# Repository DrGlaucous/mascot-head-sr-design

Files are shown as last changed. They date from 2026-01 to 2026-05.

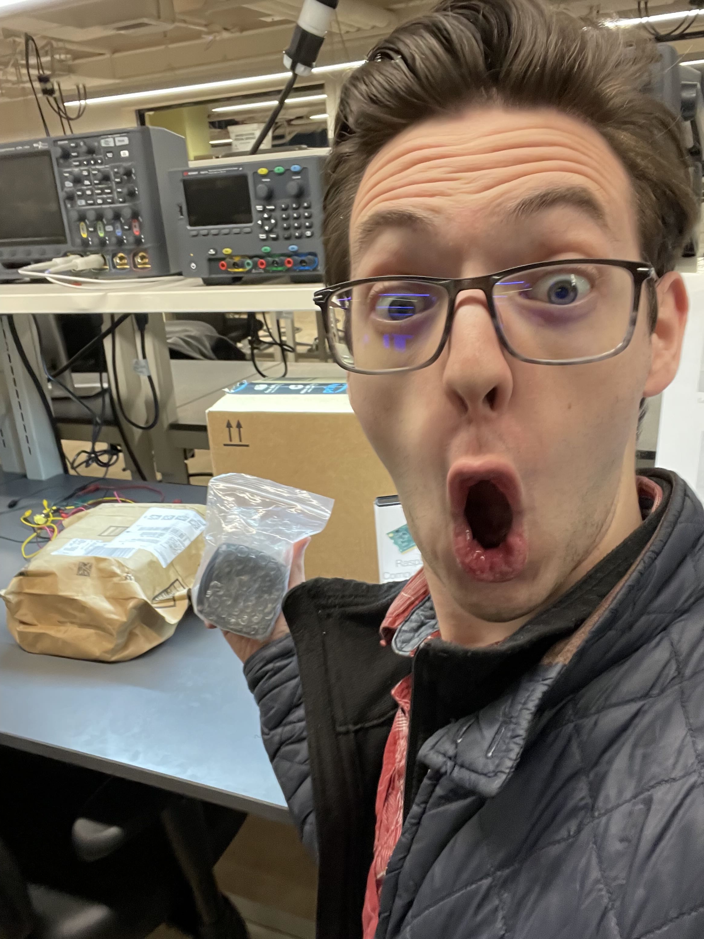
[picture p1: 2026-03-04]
redTape/going on poster.jpg

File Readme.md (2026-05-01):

# Dynamic eye mascot Sr. Design

## Locations:
- All software is in the `Software` folder
- All 3D CAD is in the `CAD` folder
- All PCB schematics are in the `Schematic` folder

## Notes

Useful info links:
- Compute io board v3: https://www.raspberrypi.com/documentation/computers/compute-module.html#cmio
- 

Things we've checked out from lab:
- x2 micro USB cables (robert)
- x1 usb TTL adapter (ed)
- x1 mini usb cable (ed)
- x1 HDMI + DP cable (robert)
- x1 Rpi3 (luis)

How to play mp3 files through the CLI:
mpg123 gives the help menu
the -f flag controls loudness (x out of 32768)

Example:
mpg123 -f 8000 JumpingJackson.mp3

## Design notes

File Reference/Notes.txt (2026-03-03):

Given 3 batteries in series with a current draw of 0.27A, 2.55 watts

started at: 4:34
9.989 V at 0:00
9.875 V at 2:00
9.716 V at 5:00
9.588 V at 7:00
9.528 V at 8:00
9.380 V at 10:00

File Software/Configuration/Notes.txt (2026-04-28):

**If OS gets corrupted again**

must copy cmdline.txt and config.txt onto the SDcard (with those names exactly). 
The good versions are in this folder, just remove the "CM4_" prefix when you copy to SDcard.

after flashing a new image onto the pi and copying the config files into the SDcard, run the pi and 
talk to it using HDMI screen and a USB keyboard. 

run this command on the Pi: sudo systemctl enable getty@ttyGS0.service
Check that it worked with: systemctl is-enabled getty@ttyGS0.service (should return "enabled")

after that, you can talk to it through serial like usual.

-----------------------------------------------

For setting up the displays and cameras, the CM3 doesn't have them enabled by default.

See this tutorial:

https://mm.digikey.com/Volume0/opasdata/d220001/medias/docus/694/Attaching_RP_Official_7in_Display_Web.pdf

The github documentation for the CM3 back when they still had it:
https://github.com/raspberrypi/documentation/tree/b4a1c04f546a82b662ad83bd408a42df48147170/hardware/computemodule
another tutorial on setting up cameras on the CM3:
https://github.com/raspberrypi/documentation/blob/b4a1c04f546a82b662ad83bd408a42df48147170/hardware/computemodule/cmio-camera.md

How to compile dts files into binaries:
https://forums.raspberrypi.com/viewtopic.php?t=171745

and these forum links for extra help:
https://forums.raspberrypi.com/viewtopic.php?t=239367
https://www.raspberrypi.com/documentation/computers/compute-module.html

-----------------------------------------------------

I had to modify audiodemo.py and software.py to work with shutdown procedures.

also, I added a proper software service file to have the pi start the program on power up.

## 3: The startup service

we use `systemctl` to run the server executable when the board starts.
We do this with a new systemd service file inside: `/etc/systemd/system/software.service`:

```ini
[Unit]
Description=Pete got them moving eyes
After=multi-user.target

[Service]
Type=simple
User=srgroup
WorkingDirectory = /home/srgroup/mascot-head-sr-design/Software/
ExecStart=/usr/bin/python /home/srgroup/mascot-head-sr-design/Software/software_ed_modify.py
Restart=always
RestartSec=5

[Install]
WantedBy=multi-user.target

```

once we add this, we can start it with:
```sh
sudo systemctl daemon-reload
sudo systemctl enable software.service
sudo systemctl start software.service
```

and stop it with:
```sh
sudo systemctl disable software.service
sudo systemctl stop software.service
```

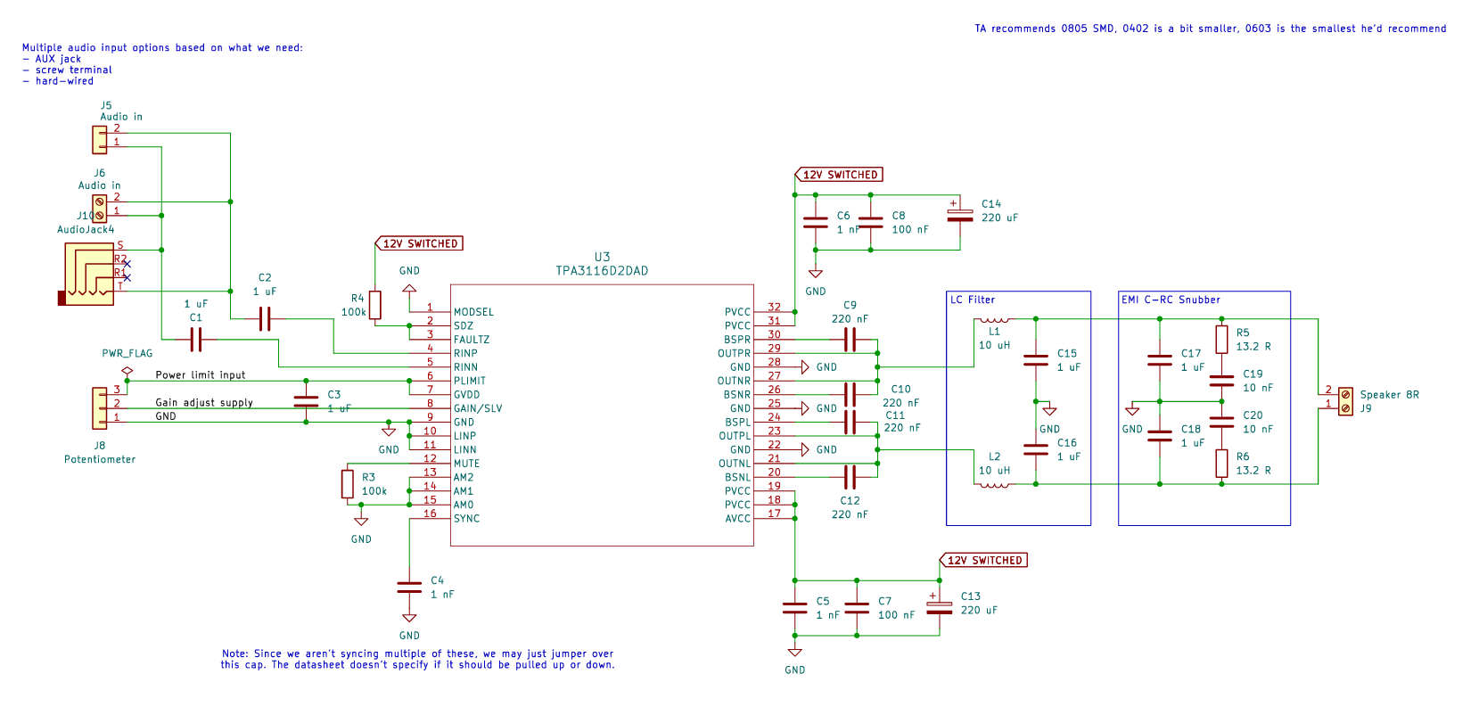
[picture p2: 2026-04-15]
RedTape/Schematic_Pics/amp.PNG

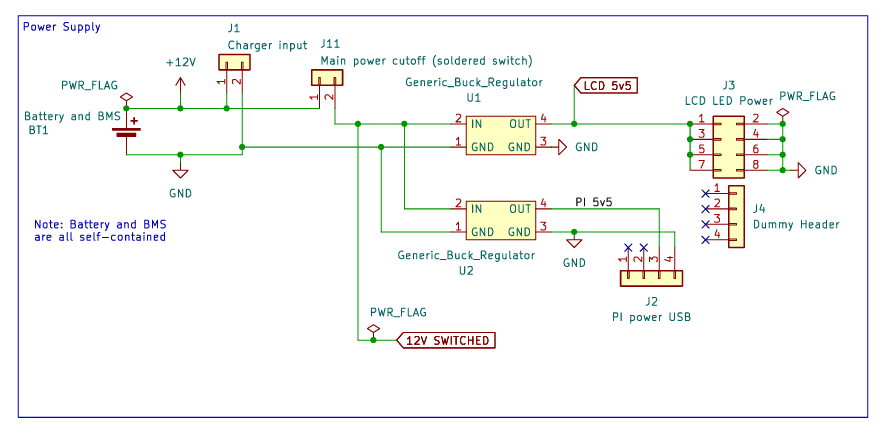
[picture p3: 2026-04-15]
RedTape/Schematic_Pics/psu.PNG

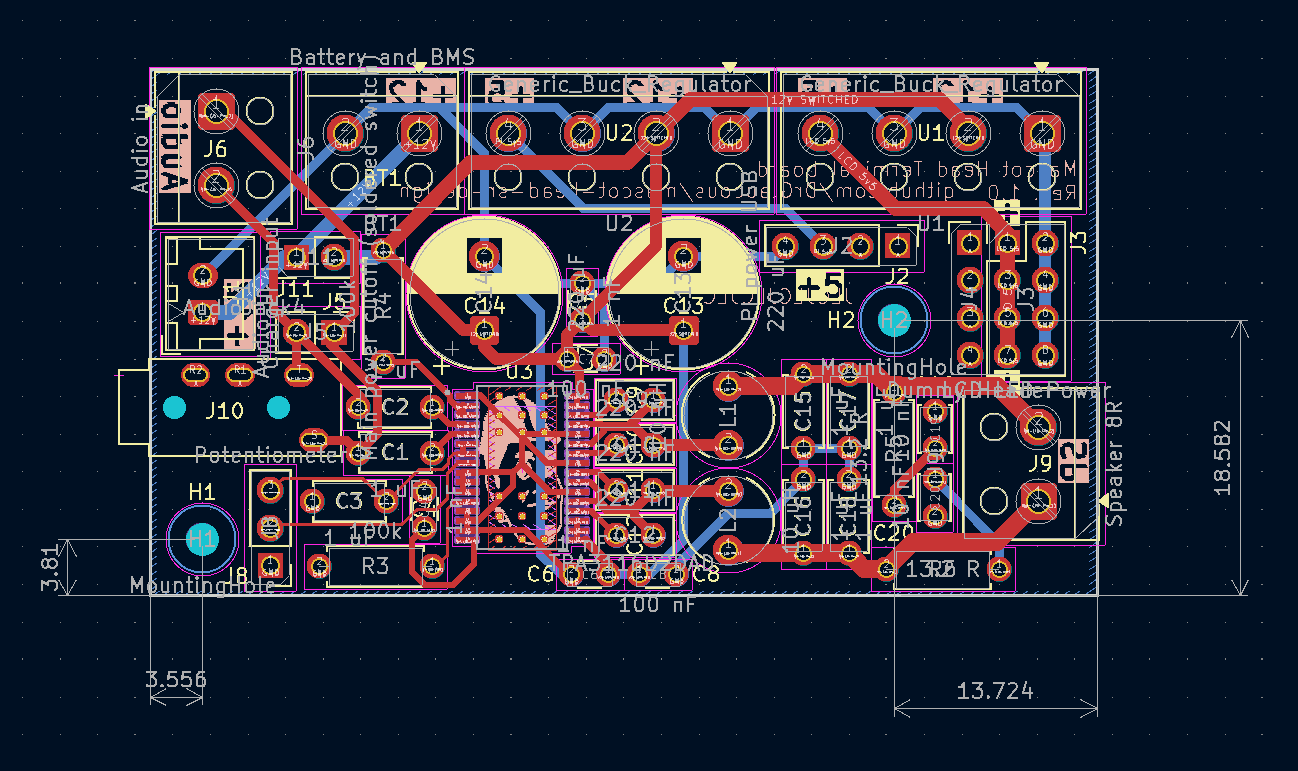
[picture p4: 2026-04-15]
RedTape/Schematic_Pics/pcb.PNG

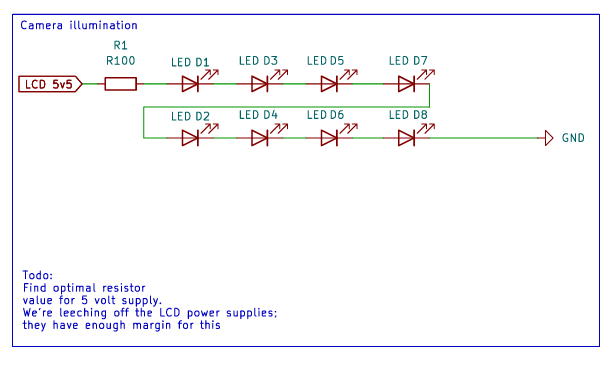
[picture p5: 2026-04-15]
RedTape/Schematic_Pics/leds.PNG

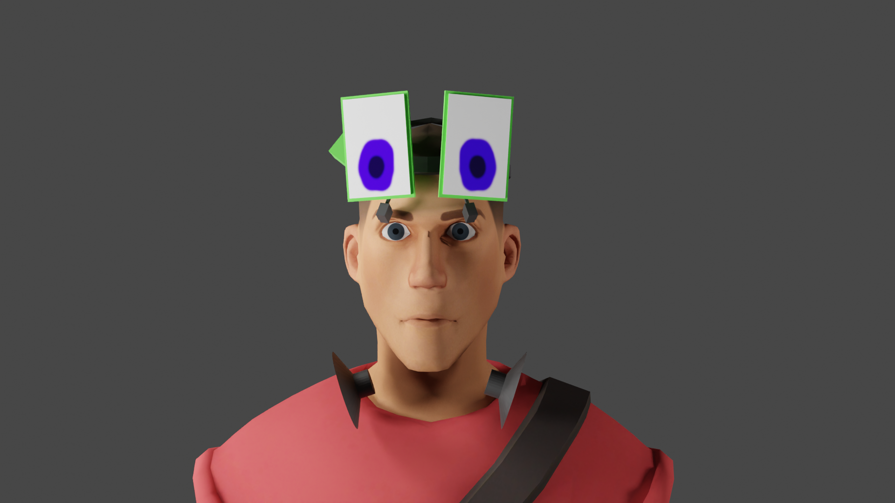
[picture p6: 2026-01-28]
Reference/scoutFront.png

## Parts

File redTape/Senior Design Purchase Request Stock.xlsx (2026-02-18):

College of Engineering Senior Design Purchase Request Form |  | Department Name: | Today's Date:
 |  | ECE | Need-By Date:
Vendor: |  | Team Name / Project: | Your Name:
Website: |  |  | Building Abbv.:
Phone Number: |  |  | Room Number:
Vendor Contact: |  | Account Number: | Phone Number:
Contact Email: |  | 7600000796 | Email Address:
ITEM NAME / PART NUMBER | DESCRIPTION & LINK |  |  | QUANTITY | UNIT COST | TOTAL COST
 |  |  |  |  | $0.00 | $0.00
 |  |  |  |  | $0.00 | $0.00
 |  |  |  |  | $0.00 | $0.00
 |  |  |  |  | $0.00 | $0.00
 |  |  |  |  | $0.00 | $0.00
 |  |  |  |  | $0.00 | $0.00
 |  |  |  |  | $0.00 | $0.00
 |  |  |  |  | $0.00 | $0.00
 |  |  |  |  | $0.00 | $0.00
 |  |  |  |  | $0.00 | $0.00
 |  |  |  |  | $0.00 | $0.00
 |  |  |  |  | $0.00 | $0.00
 |  |  |  |  | $0.00 | $0.00
 |  |  |  |  | $0.00 | $0.00
 |  |  |  |  | $0.00 | $0.00
 |  |  |  |  | $0.00 | $0.00
 |  |  |  |  | $0.00 | $0.00
 |  |  |  |  | $0.00 | $0.00
 |  |  |  |  | $0.00 | $0.00
 |  |  |  |  | $0.00 | $0.00
 |  |  |  |  | $0.00 | $0.00
Shipping / Handling |  |  |  |  | $0.00 | $0.00
Requisition Total |  |  |  |  |  | $0.00
*** ALL BLUE CELLS are Mandatory *** Do Not Alter Formulas ***

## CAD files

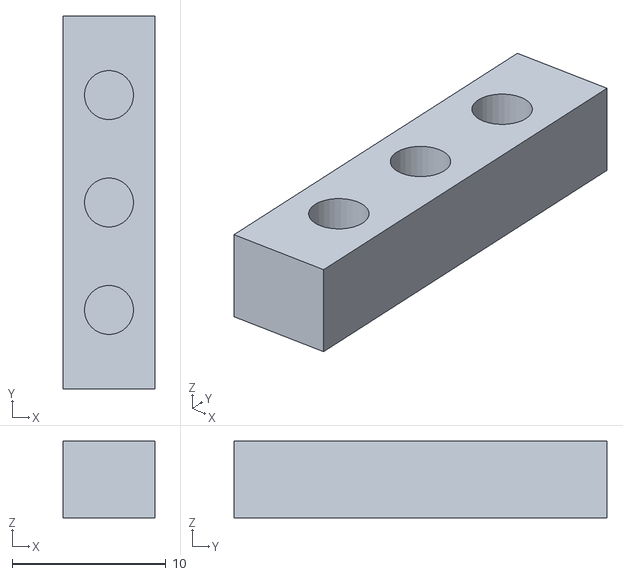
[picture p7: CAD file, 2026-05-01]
CAD/STLs/LEDHolder.stl
6.00 x 24.3 x 5.00

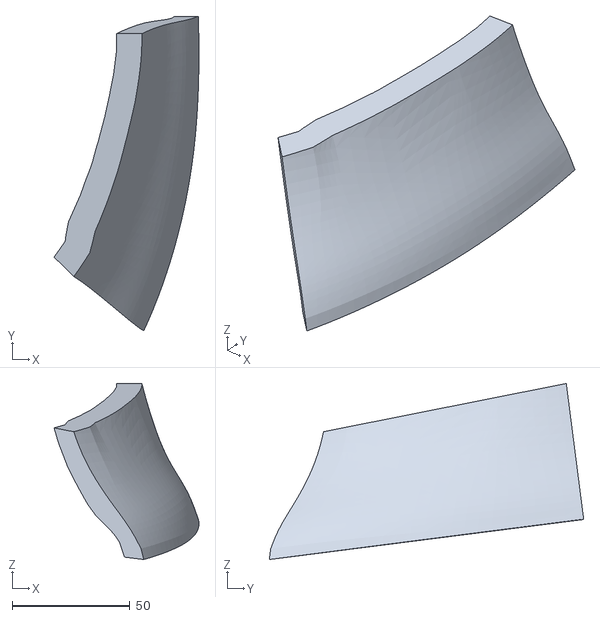
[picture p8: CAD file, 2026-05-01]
CAD/STLs/MaskParts/Hat/L/Done/Hat_L0_L.stl
61.6 x 133.7 x 74.8

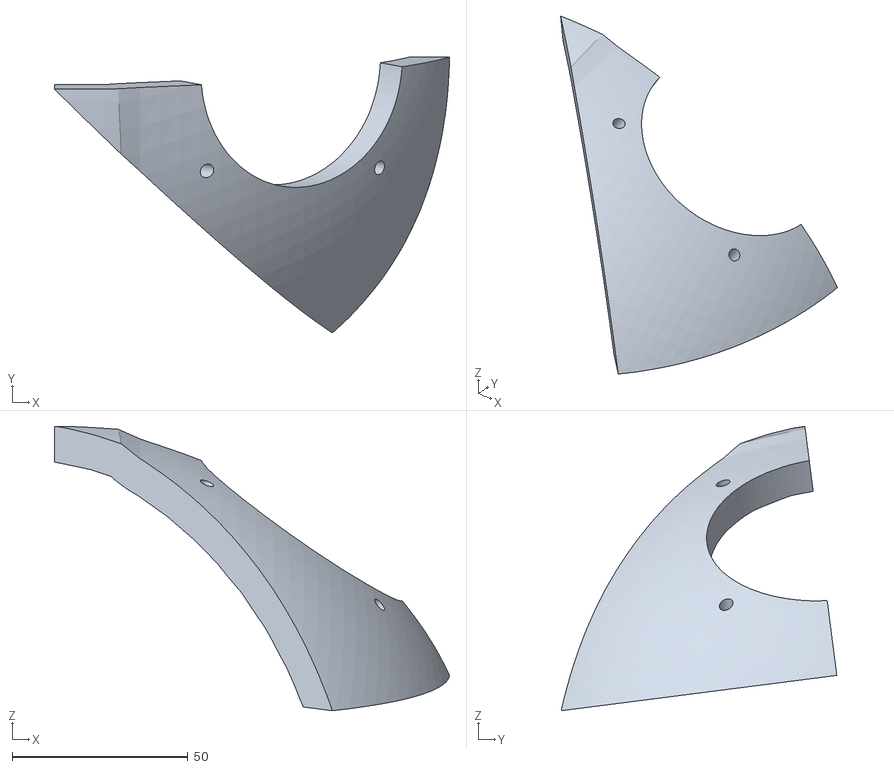
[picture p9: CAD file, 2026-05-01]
CAD/STLs/MaskParts/Hat/L/Hat_L2_L_001.stl
112.3 x 78.4 x 80.9

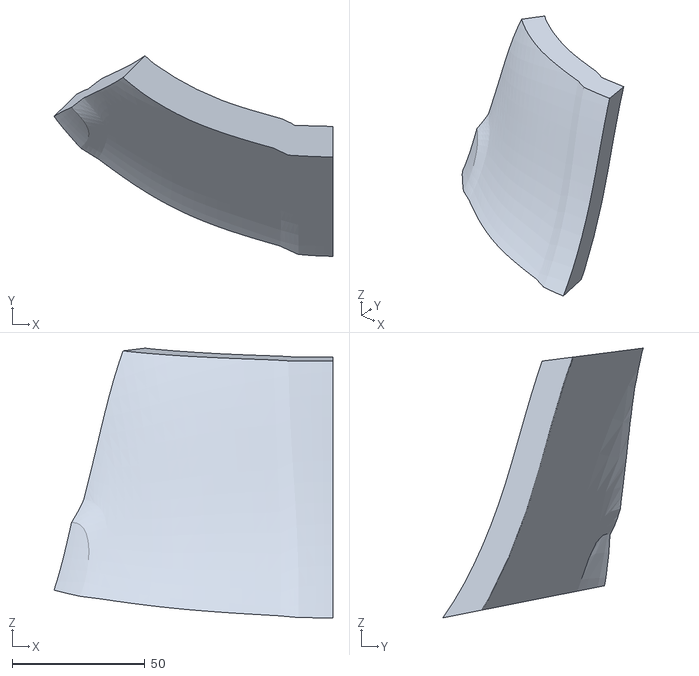
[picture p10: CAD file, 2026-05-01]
CAD/STLs/MaskParts/Hat/R/Hat_L1_R_006.stl
105.0 x 75.5 x 101.5

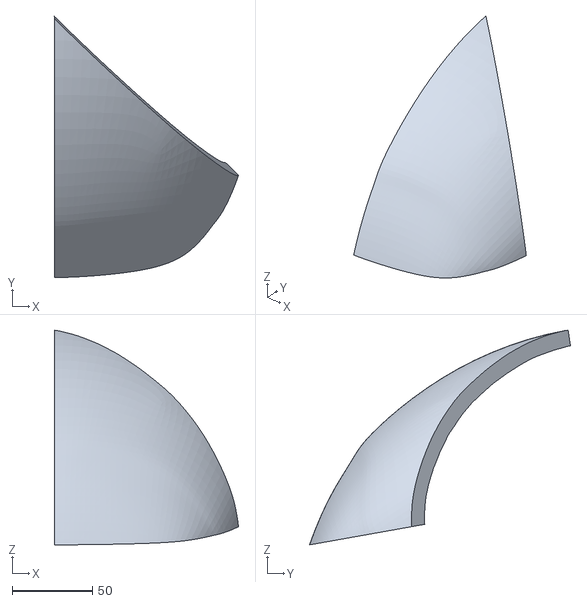
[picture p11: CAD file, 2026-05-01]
CAD/STLs/MaskParts/Left/Done/HeadSlices_L4_L_002.stl
114.9 x 163.0 x 134.1

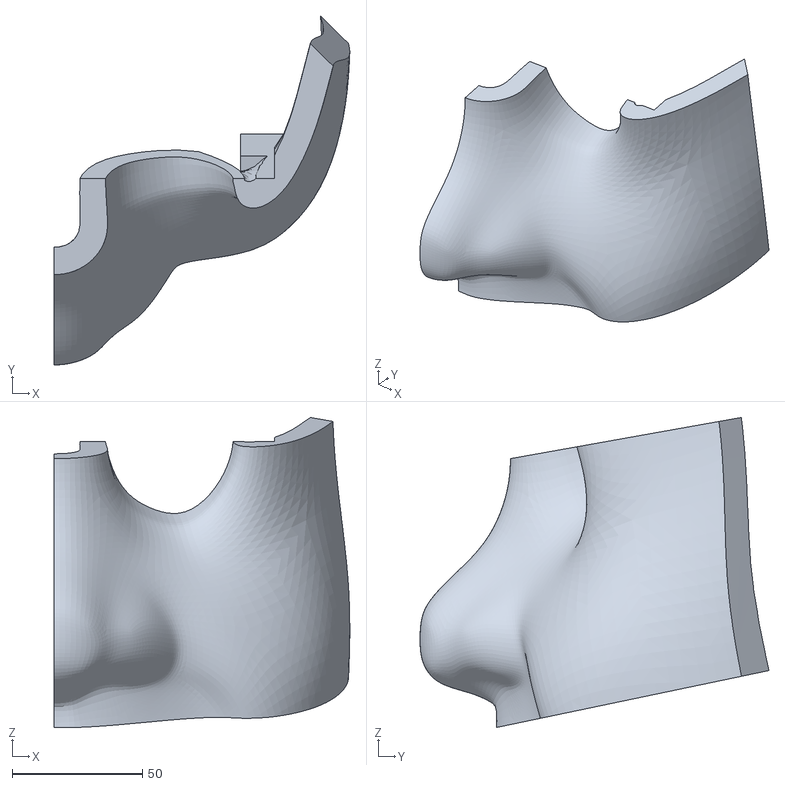
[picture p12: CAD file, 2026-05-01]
CAD/STLs/MaskParts/Left/HeadSlices_L2_L_003.stl
113.3 x 133.8 x 118.8

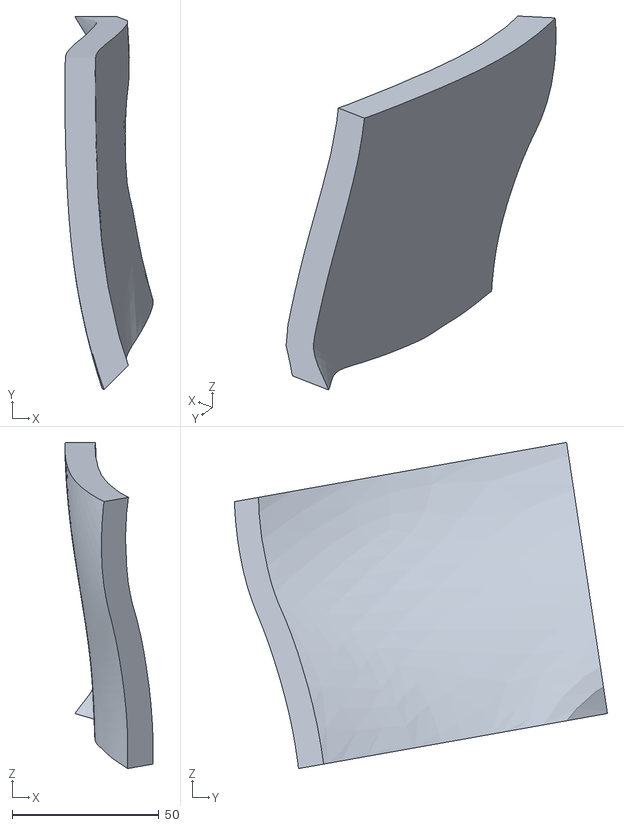
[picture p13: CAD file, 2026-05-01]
CAD/STLs/MaskParts/Right/Done/HeadSlices_L3_R_004.stl
30.1 x 127.1 x 111.2

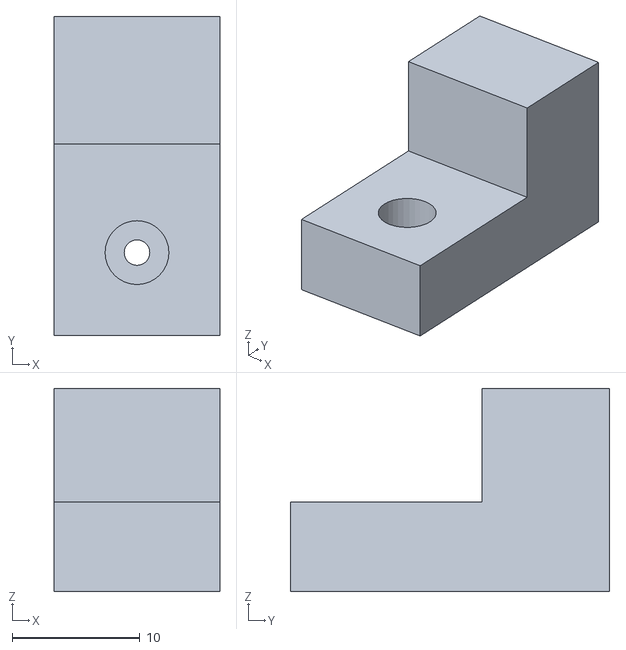
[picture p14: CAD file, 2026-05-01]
CAD/STLs/MaskParts/ScreenMountClipScreenMountClips_002.stl
13.0 x 25.0 x 15.9

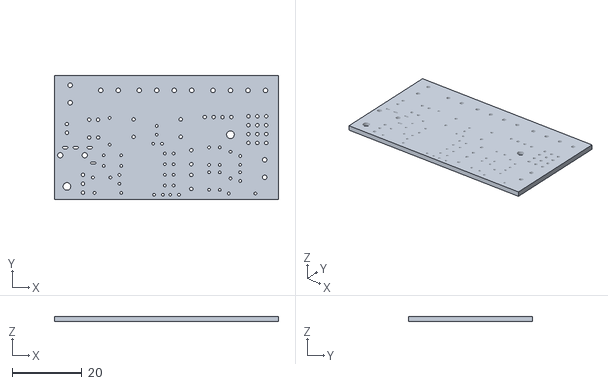
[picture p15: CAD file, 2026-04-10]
Reference/PCBV1_3d.stl
64.0 x 35.6 x 1.51

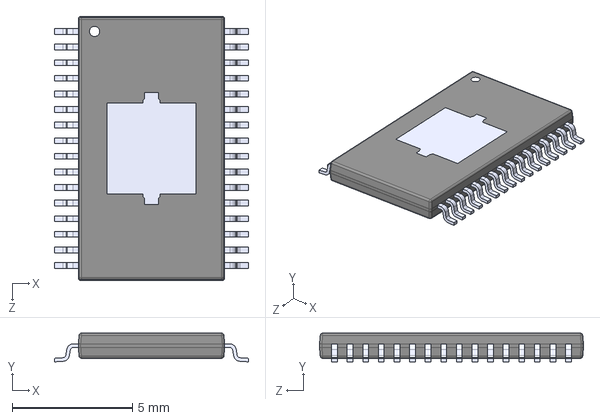
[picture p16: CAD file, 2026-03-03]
Reference/TPA3116D2DAD/TPA3116D2DAD.step
8.10 x 1.20 x 11.0 mm

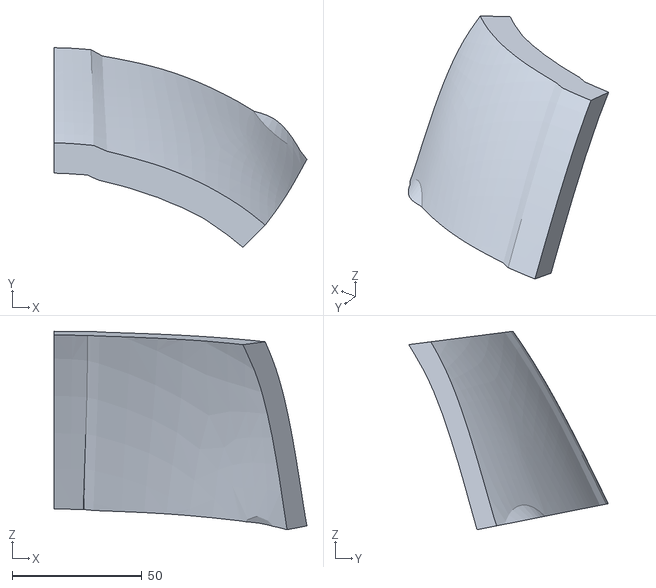
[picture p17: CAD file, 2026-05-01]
CAD/STLs/MaskParts/Hat/L/Done/Hat_L1_L.stl
97.4 x 76.9 x 76.4

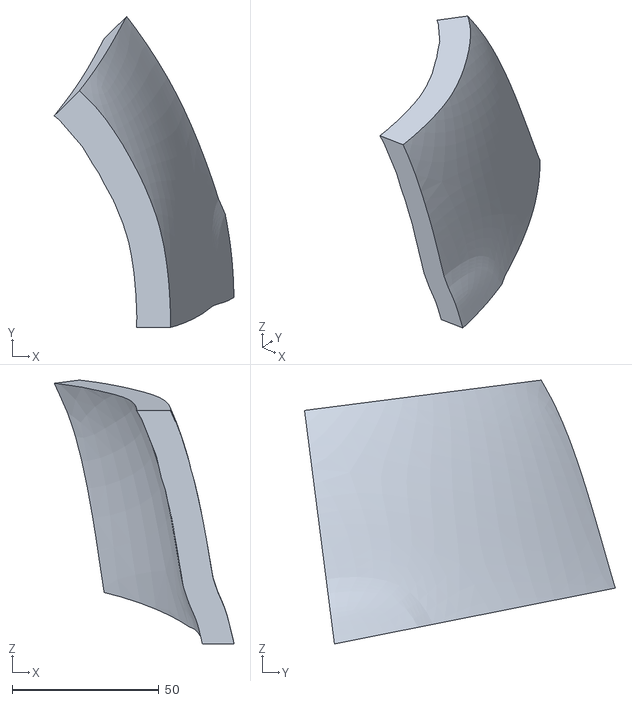
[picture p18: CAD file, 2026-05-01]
CAD/STLs/MaskParts/Hat/L/Hat_L1_L_003.stl
61.2 x 106.0 x 89.9

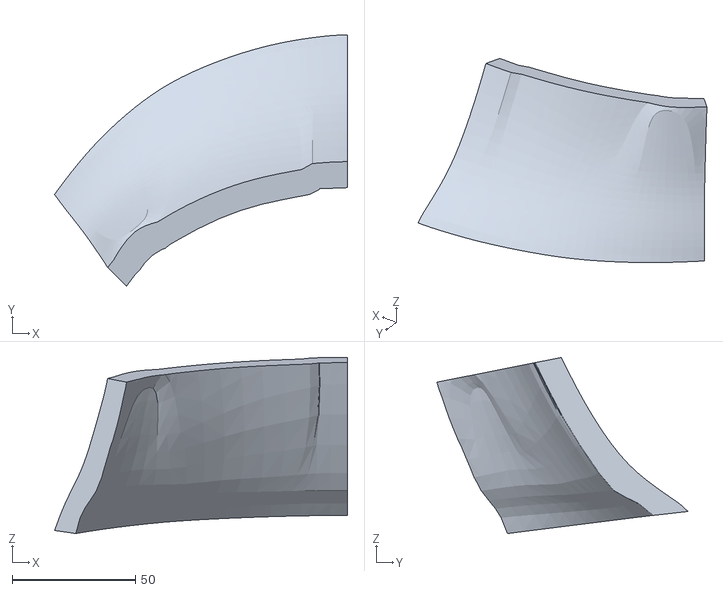
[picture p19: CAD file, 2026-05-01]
CAD/STLs/MaskParts/Hat/R/Hat_L0_R_006.stl
119.0 x 102.0 x 71.5

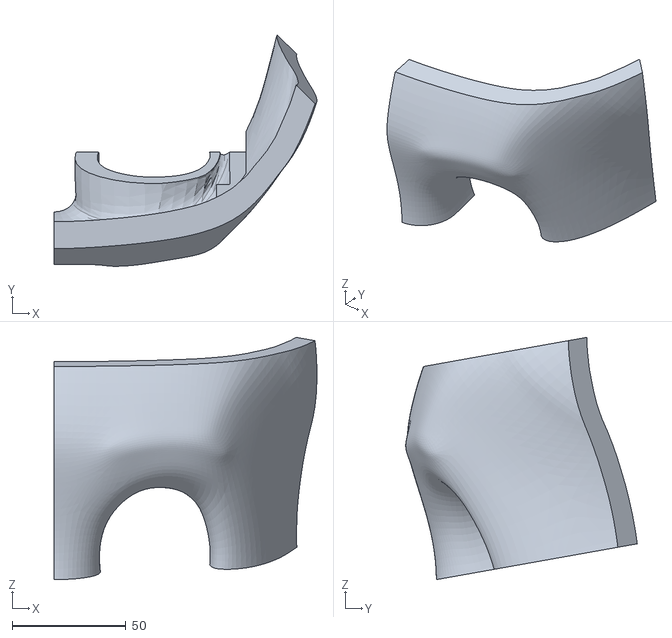
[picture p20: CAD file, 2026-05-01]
CAD/STLs/MaskParts/Left/Done/HeadSlices_L3_L_002.stl
115.8 x 102.0 x 106.7

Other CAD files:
CAD/STLs/MaskParts/Right/HeadSlices_L4_R_006.stl
CAD/STLs/MaskParts/Right/Done/HeadSlices_L1_R_004.stl
CAD/STLs/MaskParts/Right/HeadSlices_L4_R_005.stl
CAD/STLs/MaskParts/Hat/L/Done/Hat_L0_L_003.stl
CAD/STLs/CM4_Bracket.stl
CAD/STLs/CameraHolder.stl
CAD/STLs/CameraHolderBracket_L.stl
CAD/STLs/CameraHolderBracket_R.stl
CAD/STLs/ConnectorBack.stl
CAD/STLs/ConnectorScreenEdge_Center.stl
CAD/STLs/ConnectorScreenEdge_L.stl
CAD/STLs/ConnectorScreenEdge_R.stl
CAD/STLs/ConnectorScreenStripTop.stl
CAD/STLs/ConverterMountApplied.stl
CAD/STLs/MaskParts/Hat/L/Done/Hat_L0_L_001.stl
CAD/STLs/MaskParts/Hat/L/Done/Hat_L0_L_002.stl
CAD/STLs/MaskParts/Hat/L/Done/Hat_L1_L_001.stl
CAD/STLs/MaskParts/Hat/L/Done/Hat_L1_L_002.stl
CAD/STLs/MaskParts/Hat/L/Hat_L2_L.stl
CAD/STLs/MaskParts/Hat/L/Hat_L2_L_002.stl
CAD/STLs/MaskParts/Hat/L/Hat_L2_L_003.stl
CAD/STLs/MaskParts/Hat/R/Hat_L0_R_004.stl
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

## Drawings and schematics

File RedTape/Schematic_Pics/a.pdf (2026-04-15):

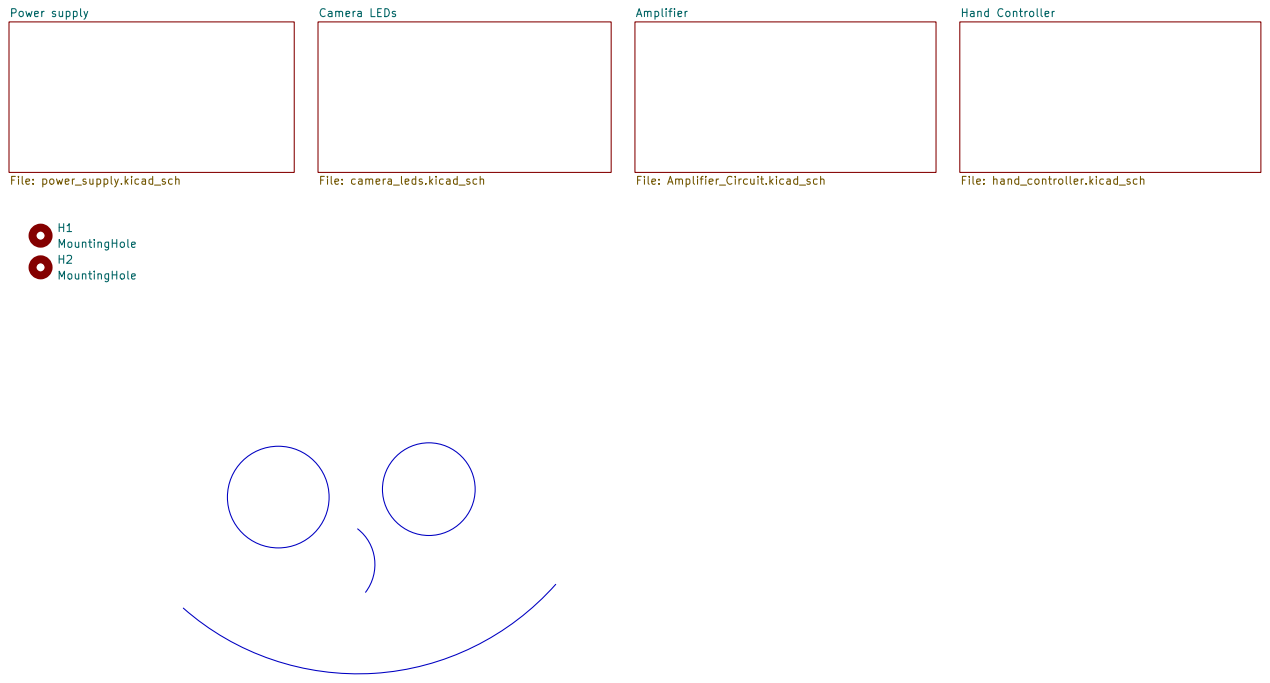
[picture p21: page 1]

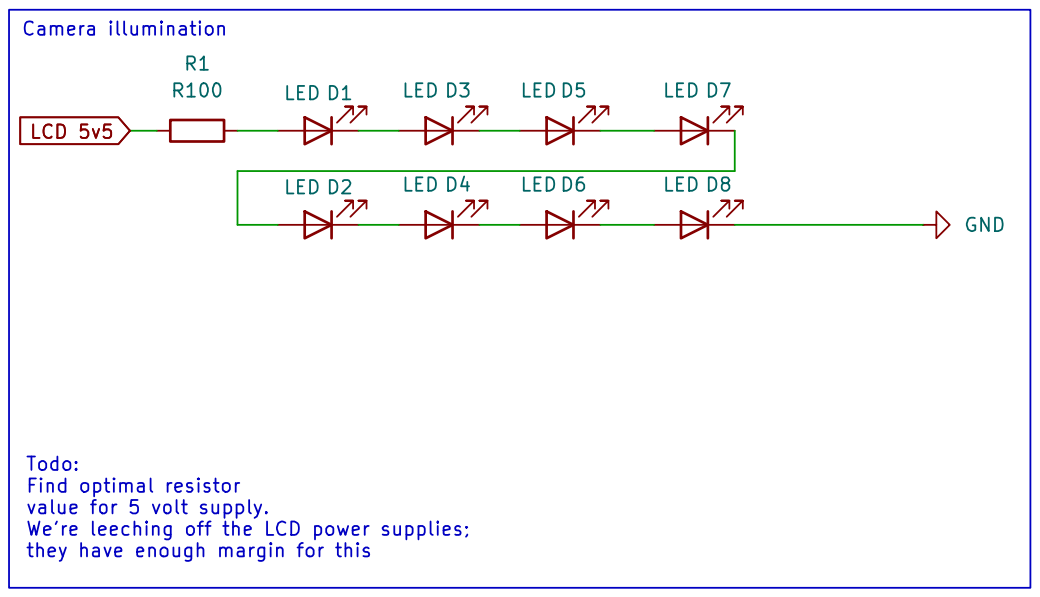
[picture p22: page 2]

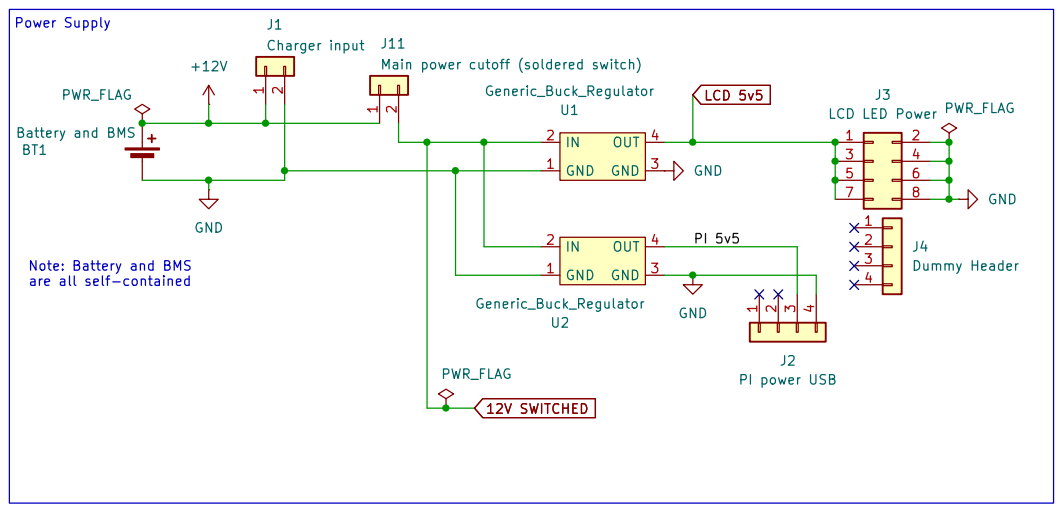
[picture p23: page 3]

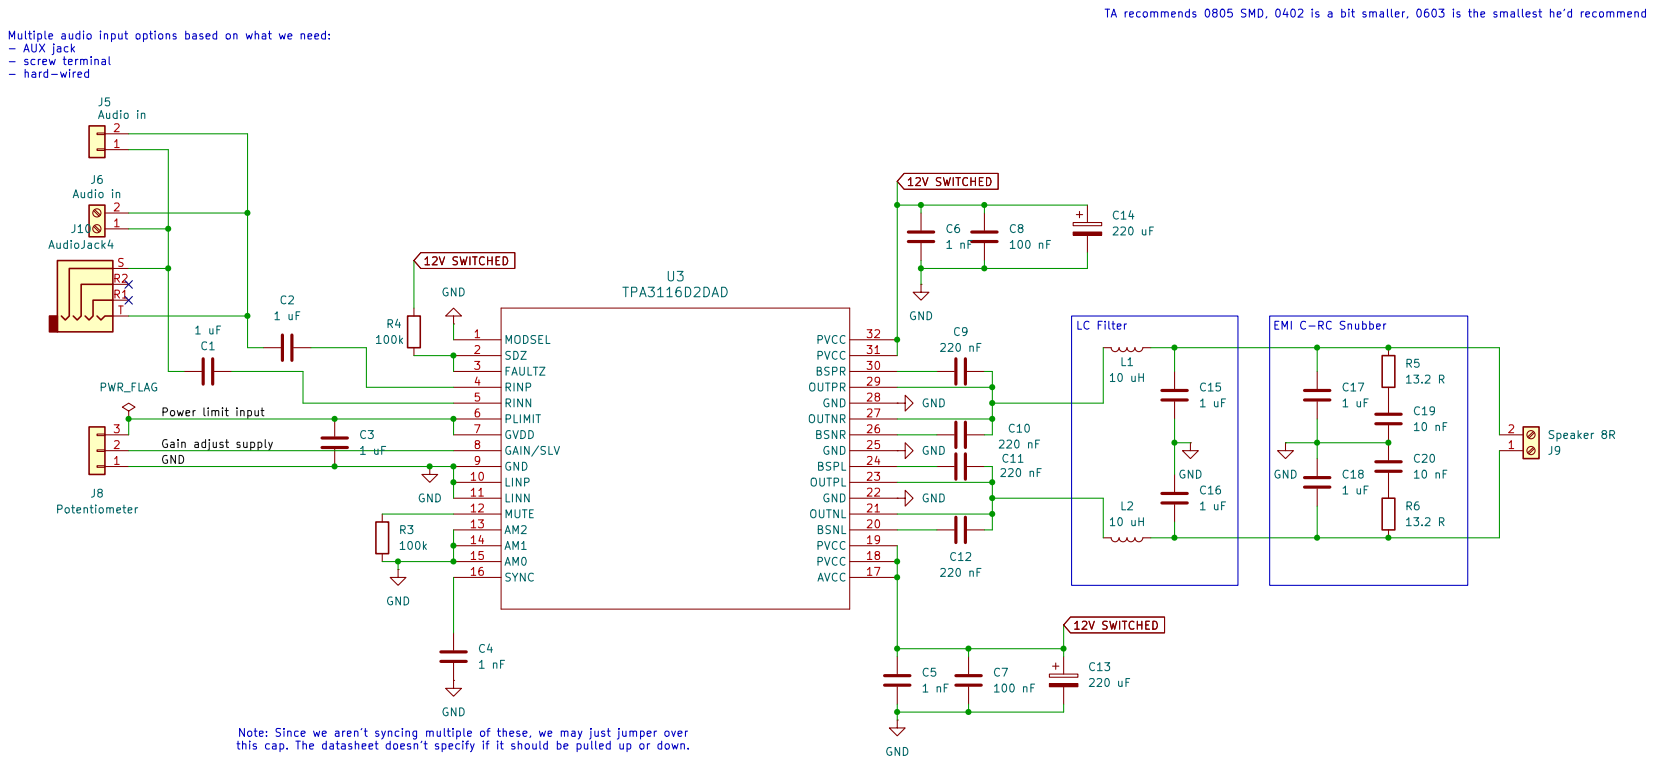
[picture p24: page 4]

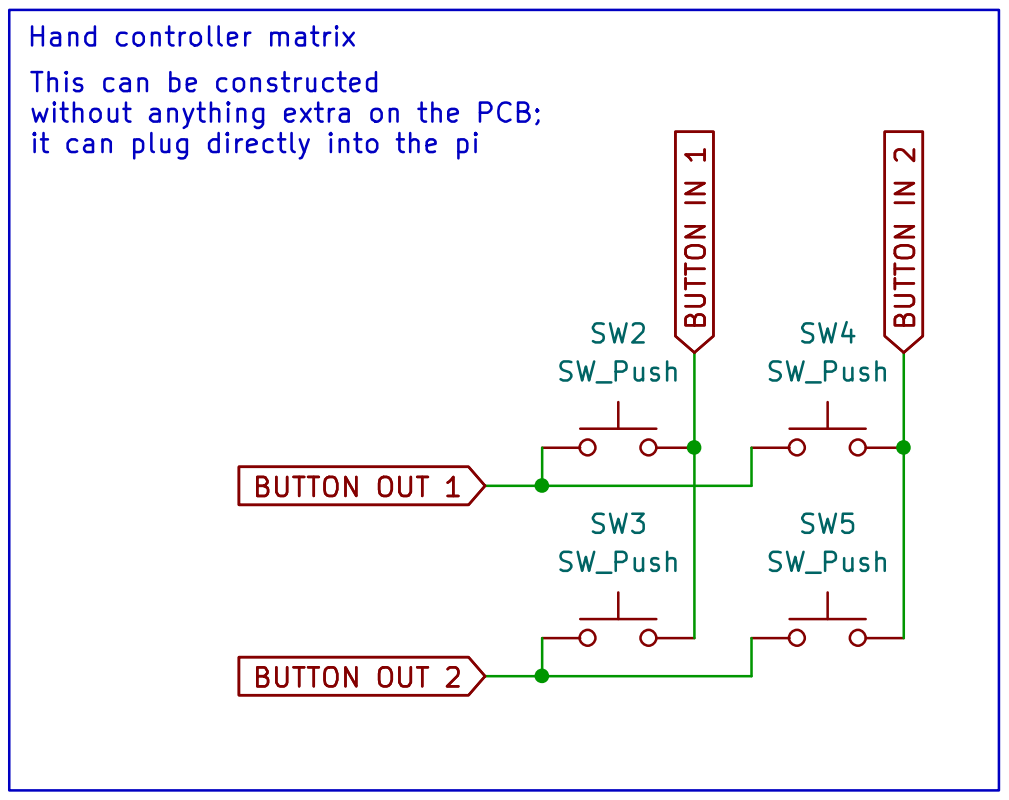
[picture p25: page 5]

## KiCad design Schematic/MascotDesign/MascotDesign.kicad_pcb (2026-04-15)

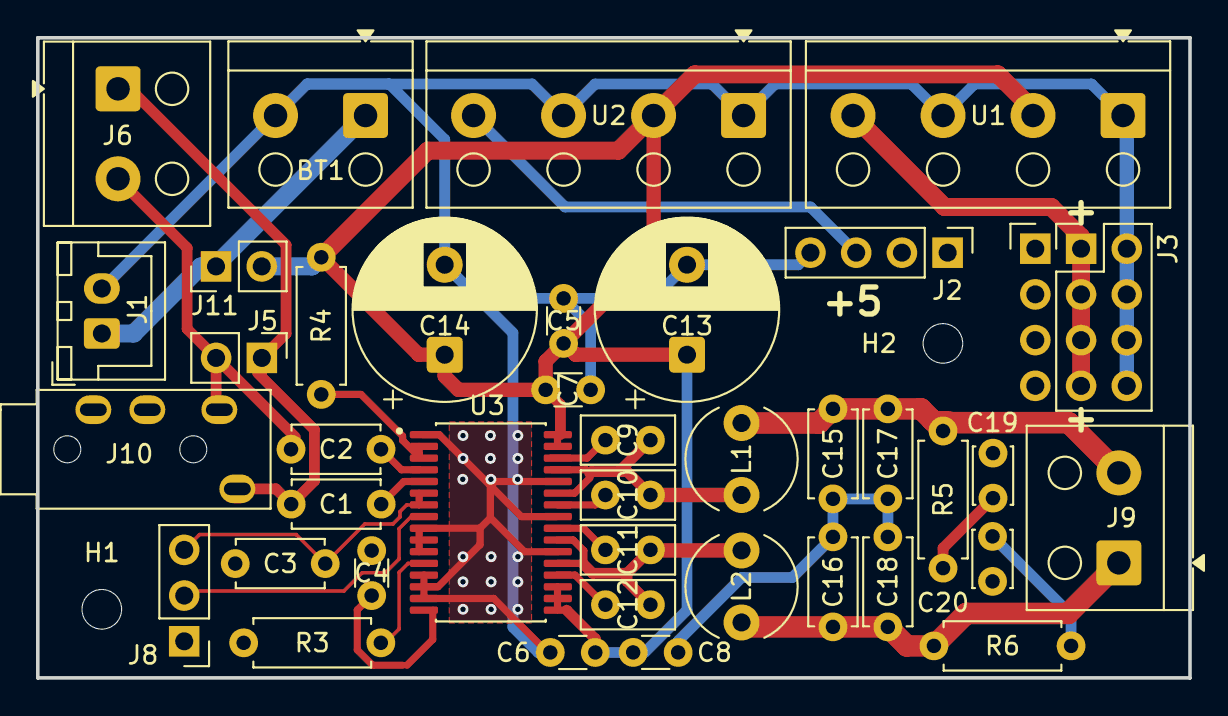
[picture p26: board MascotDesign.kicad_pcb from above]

Board: 2 copper layers, 64.0 x 35.6 mm, 42 parts (0 on the bottom side), 24 nets.

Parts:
BT1: Battery and BMS; TerminalBlock_RND_205-00001_1x02_P5.00mm_Horizontal
C1, C2, C3, C15, C16, C17, C18: 1 uF; C_Disc_D4.7mm_W2.5mm_P5.00mm
C4, C5, C6: 1 nF; C_Disc_D3.0mm_W1.6mm_P2.50mm
C7, C8: 100 nF; C_Disc_D3.0mm_W1.6mm_P2.50mm
C9, C10, C11, C12: 220 nF; C_Disc_D5.0mm_W2.5mm_P2.50mm
C13, C14: 220 uF; CP_Radial_D10.0mm_P5.00mm
C19, C20: 10 nF; C_Disc_D3.0mm_W2.0mm_P2.50mm
H1, H2: MountingHole; MountingHole_2.2mm_M2
J1: Charger input; JST_XH_B2B-XH-A_1x02_P2.50mm_Vertical
J2: PI power USB; PinHeader_1x04_P2.54mm_Vertical
J3: LCD LED Power; PinHeader_2x04_P2.54mm_Vertical
J4: Dummy Header; PinHeader_1x04_P2.54mm_Vertical
J5: Audio in; PinHeader_1x02_P2.54mm_Vertical
J6: Audio in; TerminalBlock_RND_205-00001_1x02_P5.00mm_Horizontal
J8: Potentiometer; PinHeader_1x03_P2.54mm_Vertical
J9: Speaker 8R; TerminalBlock_RND_205-00001_1x02_P5.00mm_Horizontal
J10: AudioJack4; PJ-320A
J11: Main power cutoff (soldered switch); PinHeader_1x02_P2.54mm_Vertical
L1, L2: 10 uH; L_Radial_D6.0mm_P4.00mm
R3, R4: 100k; R_Axial_DIN0207_L6.3mm_D2.5mm_P7.62mm_Horizontal
R5, R6: 13.2 R; R_Axial_DIN0207_L6.3mm_D2.5mm_P7.62mm_Horizontal
U1, U2: Generic_Buck_Regulator; TerminalBlock_RND_205-00003_1x04_P5.00mm_Horizontal
U3: TPA3116D2DAD; SOP65P810X115-32N

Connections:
12V SWITCHED: C5.1, C6.1, C7.1, C8.1, C13.1, C14.1, J11.2, R4.1, U1.2 (IN), U2.2 (IN), U3.17 (AVCC), U3.18 (PVCC), U3.19 (PVCC), U3.31 (PVCC), U3.32 (PVCC)
+12V: BT1.1 (+), J1.1, J11.1
/Amplifier/Gain adjust supply: J8.2, U3.8 (GAIN/SLV)
/Amplifier/Power limit input: C3.2, J8.3, U3.6 (PLIMIT), U3.7 (GVDD)
/Power supply/PI 5v5: J2.3, U2.4 (OUT)
GND: BT1.2 (-), C3.1, C4.2, C5.2, C6.2, C7.2, C8.2, C13.2, C14.2, C15.1, C16.2, C17.1, C18.2, C19.1, C20.2, J1.2, J2.4, J3.2, J3.4, J3.6, J3.8, J8.1, R3.2, U1.1 (GND), U1.3 (GND), U2.1 (GND), U2.3 (GND), U3.1 (MODSEL), U3.9 (GND), U3.10 (LINP), U3.11 (LINN), U3.13 (AM2), U3.14 (AM1), U3.15 (AM0), U3.22 (GND), U3.25 (GND), U3.28 (GND)
LCD 5v5: J3.1, J3.3, J3.5, J3.7, U1.4 (OUT)
unnamed: C19.2, R5.2
unnamed: C20.1, R6.1
unnamed: C1.1, J5.1, J6.1, J10.S
unnamed: C2.2, J5.2, J6.2, J10.T
unnamed: C16.1, C18.1, J9.1, L2.1, R6.2
unnamed: C15.2, C17.2, J9.2, L1.1, R5.1
unnamed: C12.2, U3.20 (BSNL)
unnamed: C10.2, U3.26 (BSNR)
unnamed: C11.2, U3.24 (BSPL)
unnamed: C9.2, U3.30 (BSPR)
unnamed: R4.2, U3.2 (SDZ), U3.3 (FAULTZ)
unnamed: R3.1, U3.12 (MUTE)
unnamed: C11.1, C12.1, L2.2, U3.21 (OUTNL), U3.23 (OUTPL)
unnamed: C9.1, C10.1, L1.2, U3.27 (OUTNR), U3.29 (OUTPR)
unnamed: C1.2, U3.5 (RINN)
unnamed: C2.1, U3.4 (RINP)
unnamed: C4.1, U3.16 (SYNC)

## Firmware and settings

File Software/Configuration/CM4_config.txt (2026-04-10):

# For more options and information see
# http://rptl.io/configtxt
# Some settings may impact device functionality. See link above for details

# Uncomment some or all of these to enable the optional hardware interfaces
# dtparam=i2c_arm=on
# dtparam=i2s=on
# dtparam=spi=on

# Enable audio (loads snd_bcm2835)
dtparam=audio=on

# Additional overlays and parameters are documented
# /boot/firmware/overlays/README

# Automatically load overlays for detected cameras
# camera_auto_detect=1

# Automatically load overlays for detected DSI displays
# display_auto_detect=1

# Automatically load initramfs files, if found
auto_initramfs=1

# Enable DRM VC4 V3D driver
dtoverlay=vc4-kms-v3d
max_framebuffers=2

# Don't have the firmware create an initial video= setting in cmdline.txt.
# Use the kernel's default instead.
disable_fw_kms_setup=1

# Run in 64-bit mode
arm_64bit=1

# Disable compensation for displays with overscan
disable_overscan=1

# Run as fast as firmware / board allows
arm_boost=1

[cm4]
# Enable host mode on the 2711 built-in XHCI USB controller.
# This line should be removed if the legacy DWC2 controller is required
# (e.g. for USB device mode) or if USB support is not required.
# otg_mode=1
dtparam=i2c_vc=on
dtoverlay=ov5647,cam0
dtoverlay=ov5647,cam1

dtoverlay=vc4-kms-dsi-7inch
dtoverlay=vc4-kms-dsi-7inch,dsi0

[cm5]
dtoverlay=dwc2,dr_mode=host

[all]
enable_uart=1
dtoverlay=dwc2

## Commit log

2026-02-18 Begin work on schematic
    This uses kicad 9.0!
    [MascotDesign.kicad_pcb, MascotDesign.kicad_sch, Senior Design Purchase Request Stock.xlsx]
2026-02-18 Work on schematic
    create power module and LED module in the master sheet
    [MascotDesign.kicad_sch]
2026-02-18 organize PCB schematic into different files
    so multiple people can edit different parts
    [MascotDesign.kicad_sch, camera_leds.kicad_sch, power_supply.kicad_sch]
2026-02-18 Unfinished audio schematic
2026-02-20 Effectively the amplifier circuit, compressed
    [49022_Audio_Basic.kicad_pcb, 49022_Audio_Basic.kicad_sch, cm108.kicad_sch]
2026-02-20 Tentative amplifier circuit
    [Amplifier_Circuit.kicad_sch]
2026-02-25 Work on power supply schematic
    [MascotDesign.kicad_sch, power_supply.kicad_sch]
2026-02-25 Work on initial CAD
    Also rename the old audio folder so we know it's not being used.
    [49022_Audio_Basic.kicad_pcb, 49022_Audio_Basic.kicad_sch, cm108.kicad_sch]
2026-02-27 fix some minor differences in amplifier circuit
    [Amplifier_Circuit.kicad_sch]
2026-02-28 Basic filter - sounds weird IMO
2026-02-28 Integrate Butterworth filter into audio demo
    Added Butterworth filter to process audio input.
2026-02-28 Update PCB schematics folder reference in README
2026-03-03 Assign footprints and begin PCB layout
    Need to check the ECE shop to see what parts we have on hand before we get too far into this, but still.
    It's a start.
    [Amplifier_Circuit.kicad_sch, MascotDesign.kicad_pcb, MascotDesign.kicad_sch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]
2026-03-05 Add sample audio
    Only WAV file I had on-hand, somehow; not sure what it is
2026-03-06 Work on CAD and schematics
    Got most of the components modeled for reference, now arranging them and creating brackets
    [Amplifier_Circuit.kicad_sch, MascotDesign.kicad_pcb, camera_leds.kicad_sch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]
2026-03-10 Do PCB layout
    I need to check our cap footprints to make sure we got the right ones.
    Other than that, the PCB should be mostly routed.
    [Amplifier_Circuit.kicad_sch, MascotDesign.kicad_pcb, camera_leds.kicad_sch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]
2026-03-10 update PCB and mounting brackets
    give PCB the correct footprints for the parts we have and add more mounting brackets for the 3D model
    [Amplifier_Circuit.kicad_sch, MascotDesign.kicad_pcb, MascotDesign.kicad_sch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]
2026-03-10 ensure board passes DRC errors
    not warnings though. Those are mostly just silkscreen overlaps.
    We need to put something funny on the silkscreen yet.
    [Amplifier_Circuit.kicad_sch, MascotDesign.kicad_pcb]
2026-03-11 Tweak PCB and make power traces slightly thicker
    They should be plenty wide for our application, but if we have room, we may as well.
    I may go back and replace the speaker output traces with fill zones later to minimize impedance.
    [MascotDesign.kicad_pcb]
2026-03-18 Add screen mounts to CAD and PCB silkscreen
    [MascotDesign.kicad_pcb]
2026-03-23 Slight PCB tweaking
    [MascotDesign.kicad_pcb, power_supply.kicad_sch]
2026-03-25 Finalize and order PCB
    Ordered through JLC, so formatting was exported to match that
    [MascotDesign-B_Cu.gbl, MascotDesign-B_Mask.gbs, MascotDesign-B_Paste.gbp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]
2026-03-25 Work on cad and upload more dts files
    Added template dts and bin files from the pi tutorial for easy access since the originals are no longer being hosted on github
    [MascotDesign.kicad_pcb]
2026-03-31 Add pi CM4 cad refrences
    Kicad, documentation, and 3d model (exported from kicad)
    [CM4IOv5-B_Cu.gbr, CM4IOv5-B_Mask.gbr, CM4IOv5-Edge_Cuts.gbr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]
2026-04-03 Clean up input_callback by removing firstTime
    Removed unused firstTime variable and related print statements.
2026-04-08 added working config files | added "stabilizedGaze" to eyeTracker
    [CM4_config.txt]
2026-04-10 Work on more CAD and schematic deisgn
    [CM4_Bracket.stl, CameraHolder.stl, CameraHolderBracket_L.stl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]
2026-04-14 Update PCB with correct TRRS pinout
    Also begin work on the actual pete mask CAD
    [Amplifier_Circuit.kicad_sch, MascotDesign.kicad_pcb, ScreenMount_ScrewSpacer.stl]
2026-04-24 Fixed butterworth filter blowing out audio
2026-04-28 Refactor audio into AudioManager object able to switch between filters
2026-05-01 Work on CAD and export head + hat slices
    [EyeHole_HeadSlices_L2_L_003.stl, EyeHole_HeadSlices_L2_R_007.stl, Hat_L0_L.stl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]
